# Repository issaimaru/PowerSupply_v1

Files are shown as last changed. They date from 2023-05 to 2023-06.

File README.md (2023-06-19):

# アズサ(Azusa)

<br>
 



<br>
この基板はJLCPCB様のFree PCB Sponsorshipにて制作しています．<br>

## Overview
  [MotorDriver-Controller_v4](https://github.com/TNCT-Mechatech/MotorDriver-Controller_v4)の機能+αと電源回路を合体させた統合型電源基板<br>
 
## Environments
&emsp;
&emsp;&emsp;
<br>

## Usage


1. [DriveUnit Bseries](https://github.com/Issaimaru/MoterDriver_v1)を使用したいチャネルのカードエッジコネクタに差し込む．<br>
1. モータードライバを差し込んだエッジコネクタと同じチャネルにモータを接続し，必要に応じて同じチャネルのコネクタにロータリーエンコーダを接続する．<br>
1. 非常停止スイッチを刺したコネクタの下にあるトグルスイッチをONに，それ以外のトグルスイッチをOFFにする．
1. XT90とUSB Type-Cからそれぞれ電源を供給し，非常停止スイッチをONにすると稼働する．
> **Note**<br>
> USB Type-C用電源を省略する方法はDescriptionsを参照<br>

## Features
<dl>
  <dt>通信プロトコル</dt>
  <dd>CAN with Flexible Data Rate(CAN FD)</dd>
  <dt>通信用コネクタ・ケーブル</dt>
  <dd>RJ-45/LANケーブル</dd>
  <dt>マイクロコンピュータ</dt>
  <dd>STM32F446RE</dd>
  <dt>特殊回路</dt>
  <dd>
  ・オートディスチャージ回路<br>
  ・車載用スローブローヒューズ

  <dt>保護回路(電源側)</dt>
  <dd>
  ・過電流保護(閾値可変)<br>
  ・ヒステリシス付き過熱保護<br>
  ・短絡保護<br>
  ・突入電流抑制<br>
  </dd>
  <dt>保護回路(信号側)</dt>
  <dd>
  ・過電圧保護<br>
  ・過電圧クランプ<br>
  ・突入電流抑制<br>
  ・過電流保護(東芝のeFuseを使用)<br>
  ・過熱保護<br>

## Descriptions
本ハードウェアの使用方法を詳しく書いていきます．<br>
質問や連絡等あれば[@TakenMaker](https://twitter.com/TakenMaker)までお願いします．<br>

### 回路図
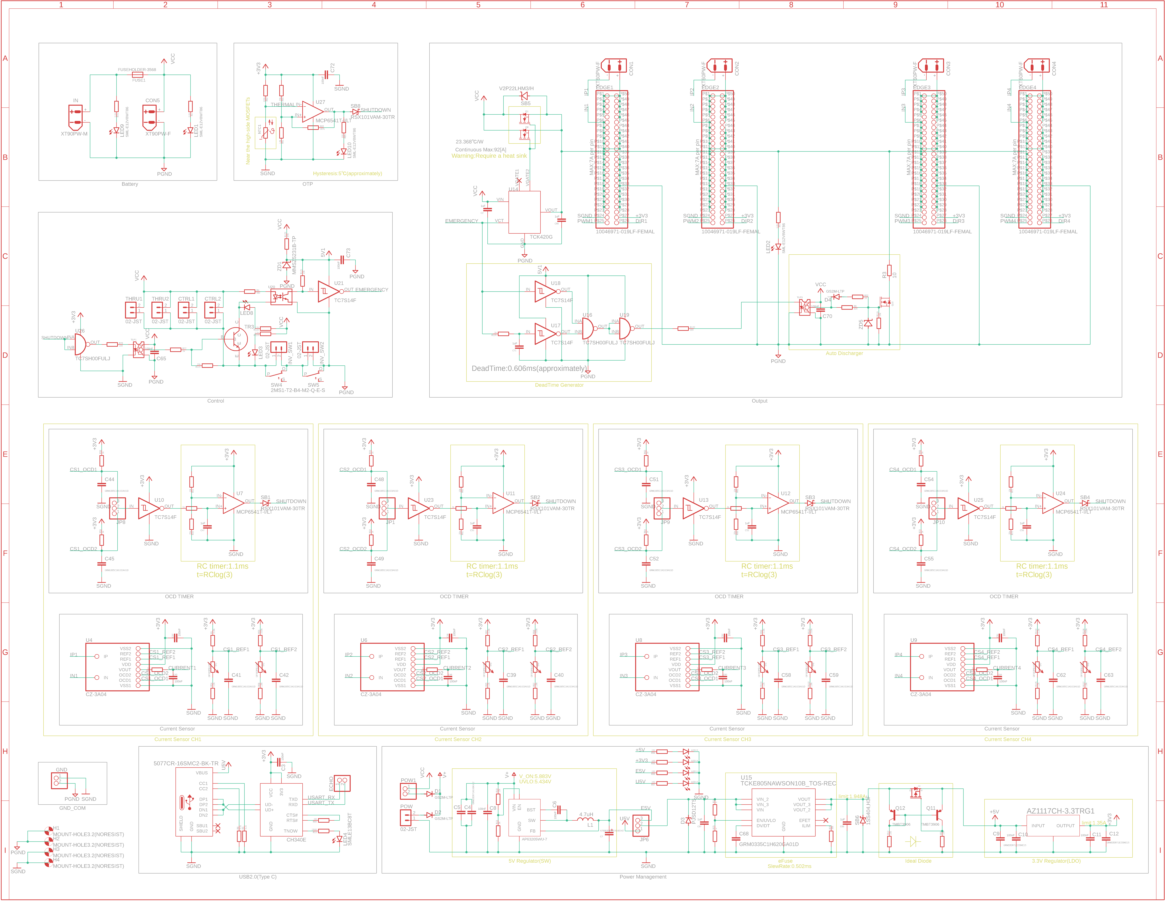
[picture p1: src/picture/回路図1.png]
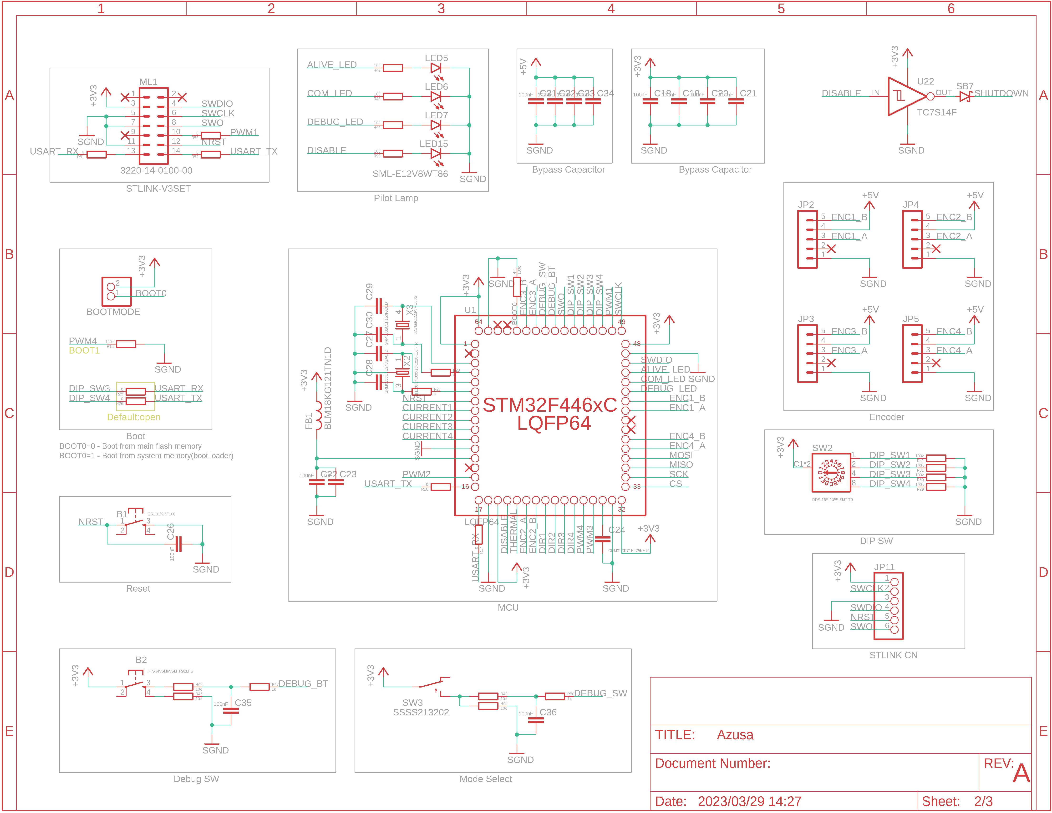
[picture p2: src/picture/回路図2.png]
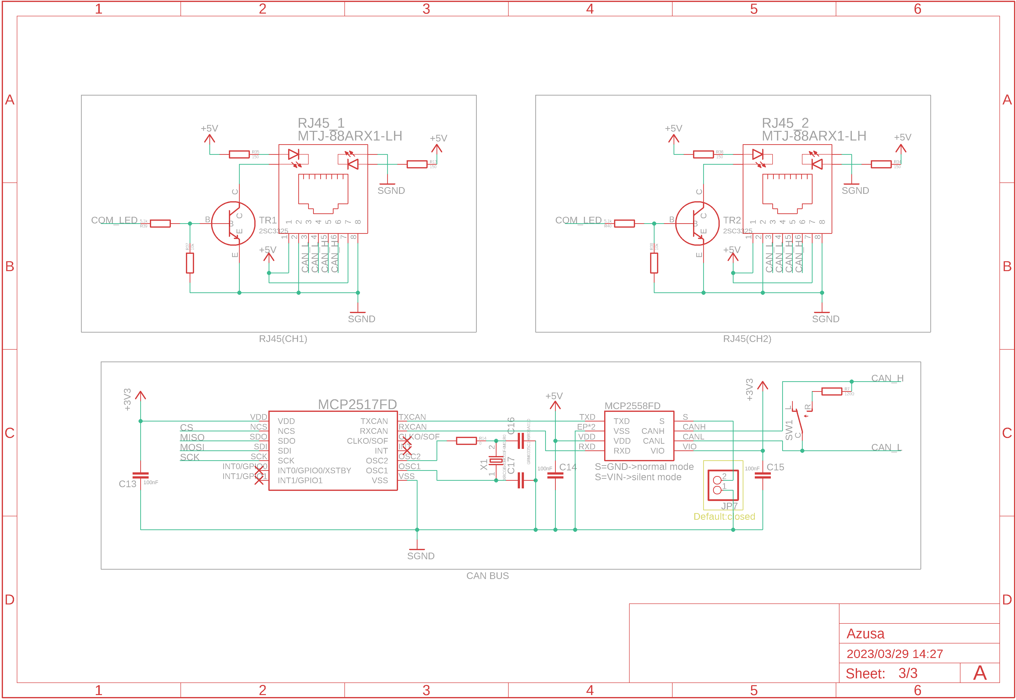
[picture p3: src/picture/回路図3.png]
&ensp;&ensp;

#### 始動方法
始動方法については[Usage](#usage)で示しました．<br>
ここでは始動時の応用的な使い方について紹介していきます．

- 信号用バッテリーの省略

<br>

JP6で信号用の電源をUSB給電or外部給電に切り替えることができます．<br>
外部電源としては，SPOWのピンに接続された電源かリポバッテリーか選ぶことができます．<br>
リポバッテリーの場合は「GND」と「SPOW」のピンヘッダを短絡してください．<br>
その際にE5VのLEDが点灯していることを確認してください．

## Bills of materials
> **Note**<br>
>最低限の部品のみここに書いています．<br>
>はんだ付けに必要な部品を調べるときは以下のexcelファイルを見るか，BOMファイルを出力してください．<br>
>[アズサ(Azusa)-ver2.0_必要部品.xlsx](src/%E3%82%A2%E3%82%BA%E3%82%B5(Azusa)-ver2.0_%E5%BF%85%E8%A6%81%E9%83%A8%E5%93%81.xlsx)
<br>
<dl>
  <dt>マイクロコンピュータ</dt>
  <dd>

  [STM32F446RET6](https://www.digikey.jp/ja/products/detail/stmicroelectronics/STM32F446RET6/5175962)

  </dd>

  <dt>電流センサ</dt>
  <dd>
  
  [CZ-3A04](https://www.digikey.jp/ja/products/detail/asahi-kasei-microdevices-akm/CZ3A04/11570562)

  </dd>
  <dt>CANトランシーバ</dt>
  <dd>

  [MCP2558FDT-H/MNY](https://www.digikey.jp/ja/products/detail/microchip-technology/MCP2558FDT-H-MNY/6009304)

  </dd>
  <dt>CANコントローラ</dt>
  <dd>

  [MCP2517FDT-H/SL](https://www.digikey.jp/ja/products/detail/microchip-technology/MCP2517FDT-H-SL/7801797)

  </dd>
  <dt>ヒートシンク</dt>
  <dd>
  
  [V2020B](https://www.digikey.jp/ja/products/detail/assmann-wsw-components/V2020B/8826902)
  
  </dd>
  <dt>ヒューズ</dt>
  <dd>

  [0297030.WXT](https://www.digikey.jp/en/products/detail/littelfuse-inc/0297030-WXT/5233697)

  </dd>
  <dt>USB・シリアル変換IC</dt>
  <dd>

  [CH340E](https://akizukidenshi.com/catalog/g/gI-13543/)

  </dd>
  <dt>NTCサーミスタ</dt>
  <dd>

  [NCU15WB473F60RC](https://www.digikey.jp/ja/products/detail/murata-electronics/NCU15WB473F60RC/9686720)

  </dd>
  <dt>DIPスイッチ</dt>
  <dd>

  [RDS-16S-1055-SMT-TR](https://www.digikey.jp/ja/products/detail/cui-devices/RDS-16S-1055-SMT-TR/12424507)

  </dd>
</dl>

## Contact
- Twitter [@TakenMaker](https://twitter.com/TakenMaker)

## Author
    
<table>
  <tr>
    <td align="center"><a href="https://github.com/Issaimaru">Issaimaru<br /></a>Issaimaru</td>
  </tr>
</table>
    
## Licence
  - Copyright © 2022-2023 Issaimaru<br>

本ハードウェアは，Apache License Version 2.0の下で配布されます．<br>
詳しくはLICENSEファイルをご確認ください．<br>

## 回路図のダウンロード(クローン)方法
1. Gitをインストールする．<br>Gitのインストール方法は[ここ](https://www.sejuku.net/blog/73444)を参照．
1. コマンドプロンプトを立ち上げる．
1. `cd ”ダウンロード先フォルダの絶対パス” `<br>
1. `git clone https://github.com/Issaimaru/PowerSupply_v1.git`<br>

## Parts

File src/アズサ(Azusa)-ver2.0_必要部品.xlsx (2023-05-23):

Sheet: 継続紙
財源（該当欄にチェックしてください） □授業料収入 □寄付金 □科学研究費 □受託研究 □共同研究 □運営費交付金 □
備考（予算科目等）
 | 請求者： |  |  |  | 納入場所：
品目（事項） 役務等の場合はその具体的内容 | 規格（内容） 規格は詳細に記入して下さい | 数量 |  | 単価 | 金額 | 備考
GCM188L81H104KA57 | 490-6049-1-ND | 100 | 個 | 8.81 | 881 | https://www.digikey.jp/ja/products/detail/murata-electronics/GCM188L81H104KA57D/2591908
GRM1885C1H102JA01D | 490-1451-1-ND | 100 | 個 | 3.12 | 312 | GRM1885C1H102JA01D Murata Electronics | コンデンサ | DigiKey (https://www.digikey.jp/ja/products/detail/murata-electronics/GRM1885C1H102JA01D/586943)
CR0603-JW-102ELF | CR0603-JW-102ELFCT-ND | 100 | 個 | 1.300 | 130 | CR0603-JW-102ELF Bourns Inc. | 抵抗器 | DigiKey (https://www.digikey.jp/ja/products/detail/bourns-inc/CR0603-JW-102ELF/3741004)
CR0603-JW-103ELF | CR0603-JW-103ELFCT-ND | 100 | 個 | 1.300 | 130 | https://www.digikey.jp/en/products/detail/bourns-inc/CR0603-JW-103ELF/3593214
SML-E12V8WT86 | 通販コード:I-11879 | 7 | パック | 140.000 | 980 | https://akizukidenshi.com/catalog/g/gI-11879/
CR0603-J/-000ELF | CR0603-J/-000ELFCT-ND | 100 | 個 | 0.760 | 76 | https://www.digikey.jp/ja/products/detail/bourns-inc/CR0603-J-000ELF/3593211
GRM21BC72A105KE01L | 490-14464-1-ND | 100 | 個 | 21.390 | 2139 | https://www.digikey.jp/en/products/detail/murata-electronics/GRM21BC72A105KE01L/6606093
シュミットトリガインバータ ＴＣ７Ｓ１４Ｆ | 通販コード:I-14737 | 8 | 個 | 60.000 | 480 | https://akizukidenshi.com/catalog/g/gI-14737/
半固定ボリューム ＧＦ０６３Ｐ | 通販コード:P-14905 | 50 | 個 | 30.000 | 1500 | 半固定ボリューム ＧＦ０６３Ｐ １０ｋΩ: パーツ一般 秋月電子通商-電子部品・ネット通販 (akizukidenshi.com) (https://akizukidenshi.com/catalog/g/gP-14905/)
CR0603-JW-151ELF | CR0603-JW-151ELFCT-ND | 100 | 個 | 1.410 | 141 | CR0603-JW-151ELF Bourns Inc. | 抵抗器 | DigiKey (https://www.digikey.jp/ja/products/detail/bourns-inc/CR0603-JW-151ELF/3784293)
CR0603-JW-104ELF | CR0603-JW-104ELFCT-ND | 100 | 個 | 0.760 | 76 | CR0603-JW-104ELF Bourns Inc. | 抵抗器 | DigiKey (https://www.digikey.jp/ja/products/detail/bourns-inc/CR0603-JW-104ELF/2345098)
CR0603-JW-101ELF | CR0603-JW-101ELFCT-ND | 100 | 個 | 1.300 | 130 | CR0603-JW-101ELF Bourns Inc. | 抵抗器 | DigiKey (https://www.digikey.jp/ja/products/detail/bourns-inc/CR0603-JW-101ELF/3741003)
RSX101VAM-30TR | 通販コード:RSX101VAM-30TR | 2 | 個 | 180.000 | 360 | ショットキーバリアダイオード ＲＳＸ１０１ＶＡＭ－３０ ３０Ｖ１Ａ（２０個入）: 半導体(モジュール) 秋月電子通商-電子部品・ネット通販 (akizukidenshi.com) (https://akizukidenshi.com/catalog/g/gI-05951/)
MCP6541T-I/LT | MCP6541T-I/LTCT-ND | 100 | 個 | 48.990 | 4899 | MCP6541T-I/LT Microchip Technology | Integrated Circuits (ICs) | DigiKey (https://www.digikey.jp/en/products/detail/microchip-technology/MCP6541T-I-LT/551750)
CR0603-JW-112ELF | CR0603-JW-112ELFCT-ND | 100 | 個 | 1.410 | 141 | CR0603-JW-112ELF Bourns Inc. | 抵抗器 | DigiKey (https://www.digikey.jp/ja/products/detail/bourns-inc/CR0603-JW-112ELF/3784271)
CR0603-JW-512ELF | 118-CR0603-JW-512ELFCT-ND | 100 | 個 | 1.410 | 141 | CR0603-JW-512ELF Bourns Inc. | 抵抗器 | DigiKey (https://www.digikey.jp/ja/products/detail/bourns-inc/CR0603-JW-512ELF/3784394)
CR0603-J/-3R3ELF | CR0603-J/-3R3ELFCT-ND | 100 | 個 | 1.410 | 141 | https://www.digikey.jp/ja/products/detail/bourns-inc/CR0603-J-3R3ELF/3784247
CR0603-JW-203ELF | CR0603-JW-203ELFCT-ND | 100 | 個 | 1.410 | 141 | https://www.digikey.jp/ja/products/detail/bourns-inc/CR0603-JW-203ELF/3741006
CR0603-FX-1582ELF | CR0603-FX-1582ELFCT-ND | 100 | 個 | 1.050 | 105 | CR0603-FX-1582ELF Bourns Inc. | 抵抗器 | DigiKey (https://www.digikey.jp/ja/products/detail/bourns-inc/CR0603-FX-1582ELF/3783757)
CR0603-FX-1182ELF | 118-CR0603-FX-1182ELFCT-ND | 100 | 個 | 1.480 | 148 | CR0603-FX-1182ELF Bourns Inc. | 抵抗器 | DigiKey (https://www.digikey.jp/ja/products/detail/bourns-inc/CR0603-FX-1182ELF/3783693)
CR0603-JW-162ELF | CR0603-JW-162ELFCT-ND | 100 | 個 | 1.410 | 141 | CR0603-JW-162ELF Bourns Inc. | 抵抗器 | DigiKey (https://www.digikey.jp/ja/products/detail/bourns-inc/CR0603-JW-162ELF/3784303)
CR0603-JW-122ELF | 118-CR0603-JW-122ELFCT-ND | 100 | 個 | 1.050 | 105 | CR0603-JW-122ELF Bourns Inc. | 抵抗器 | DigiKey (https://www.digikey.jp/ja/products/detail/bourns-inc/CR0603-JW-122ELF/3784278)
TC7SH00FULJ(CB | 通販コード:I-15748 | 2 | 個 | 100.000 | 200 | ２入力ＮＡＮＤ ＴＣ７ＳＨ００ＦＵ（１０個入）: 半導体(モジュール) 秋月電子通商-電子部品・ネット通販 (akizukidenshi.com) (https://akizukidenshi.com/catalog/g/gI-15748/)
SQJA16EP-T1_GE3 | 742-SQJA16EP-T1_GE3CT-ND | 15 | 個 | 198.900 | 2983.5 | SQJA16EP-T1_GE3 Vishay Siliconix | ディスクリート半導体製品 | DigiKey (https://www.digikey.jp/ja/products/detail/vishay-siliconix/SQJA16EP-T1-GE3/14542661)
GS2M-LTP | GS2M-LTPMSCT-ND | 20 | 個 | 31.700 | 634 | GS2M-LTP Micro Commercial Co | ディスクリート半導体製品 | DigiKey (https://www.digikey.jp/ja/products/detail/micro-commercial-co/GS2M-LTP/3775006)
２ＳＣ３３２５－Ｙ ５０Ｖ５００ｍＡ | 通販コード:I-00628 | 1 | 個 | 100.000 | 100 | チップトランジスタ ２ＳＣ３３２５－Ｙ ５０Ｖ５００ｍＡ （２０個入）: 半導体(モジュール) 秋月電子通商-電子部品・ネット通販 (akizukidenshi.com) (https://akizukidenshi.com/catalog/g/gI-00628/)
TMBT3906,LM | TMBT3906LMCT-ND | 10 | 個 | 22.700 | 227 | TMBT3906,LM Toshiba Semiconductor and Storage | Discrete Semiconductor Products | DigiKey (https://www.digikey.jp/en/products/detail/toshiba-semiconductor-and-storage/TMBT3906-LM/5403461)
TLP152(TPL_E | 通販コード:I-10824 | 10 | 個 | 80.000 | 800 | フォトカプラ ＧａＡｌＡｓ赤外ＬＥＤ＋フォトＩＣ ＴＬＰ１５２: 半導体(モジュール) 秋月電子通商-電子部品・ネット通販 (akizukidenshi.com) (https://akizukidenshi.com/catalog/g/gI-10824/)
GRM32ER71H106KA12 | 通販コード:P-16113 | 2 | 個 | 200.000 | 400 | チップ積層セラミックコンデンサー １０μＦ５０Ｖ Ｘ７Ｒ ３２２５ （５個入）: パーツ一般 秋月電子通商-電子部品・ネット通販 (akizukidenshi.com) (https://akizukidenshi.com/catalog/g/gP-16113/)
GRM32ER71E226KE15 | 通販コード:P-06047 | 2 | 個 | 250.000 | 500 | チップ積層セラミックコンデンサー ２２μＦ２５Ｖ Ｘ７Ｒ ３２２５ （５個入）: パーツ一般 秋月電子通商-電子部品・ネット通販 (akizukidenshi.com) (https://akizukidenshi.com/catalog/g/gP-06047/)
GRM0335C1H6R0BA01D | 490-11339-1-ND | 10 | 個 | 2.200 | 22 | GRM0335C1H6R0BA01D Murata Electronics | Capacitors | DigiKey (https://www.digikey.jp/en/products/detail/murata-electronics/GRM0335C1H6R0BA01D/4358772)
GRM0335C1H150FA01D | 490-GRM0335C1H150FA01DCT-ND | 10 | 個 | 4.600 | 46 | GRM0335C1H150FA01D Murata Electronics | Capacitors | DigiKey (https://www.digikey.jp/en/products/detail/murata-electronics/GRM0335C1H150FA01D/11618577)
GRM0335C1E240GA01D | 490-11289-1-ND | 10 | 個 | 1.800 | 18 | GRM0335C1E240GA01D Murata Electronics | Capacitors | DigiKey (https://www.digikey.jp/en/products/detail/murata-electronics/GRM0335C1E240GA01D/4358594)
2MS1-T2-B4-M2-Q-E-S | 通販コード:P-12406 | 10 | 個 | 90.000 | 900 | 基板用小型３Ｐトグルスイッチ １回路２接点: パーツ一般 秋月電子通商-電子部品・ネット通販 (akizukidenshi.com) (https://akizukidenshi.com/catalog/g/gP-12406/)
XRCGB40M000F4M01R0 | 通販コード:490-18350-1-ND | 10 | 個 | 35.200 | 352 | XRCGB40M000F4M01R0 Murata Electronics | 水晶発振器、発振器、共振器 | DigiKey (https://www.digikey.jp/ja/products/detail/murata-electronics/XRCGB40M000F4M01R0/9959707)
V2P22LHM3/H | 112-V2P22LHM3/HCT-ND | 10 | 個 | 46.800 | 468 | V2P22LHM3/H Vishay General Semiconductor - Diodes Division | Discrete Semiconductor Products | DigiKey (https://www.digikey.jp/en/products/detail/vishay-general-semiconductor-diodes-division/V2P22LHM3-H/10638949)
TLP293(BLL-TPLE(T | 通販コード:I-16783 | 2 | 個 | 120.000 | 240 | https://akizukidenshi.com/catalog/g/gI-16783/
TCK420G,L3F | 264-TCK420GL3FCT-ND | 10 | 個 | 104.800 | 1048 | TCK420G,L3F Toshiba Semiconductor and Storage | Integrated Circuits (ICs) | DigiKey (https://www.digikey.jp/en/products/detail/toshiba-semiconductor-and-storage/TCK420G-L3F/16516790)
SSSS213202 | 通販コード:P-05043 | 1 | 個 | 330.000 | 330 | 表面実装用スライドスイッチ ＳＳＳＳ２１３２０２ （１０個入）: パーツ一般 秋月電子通商-電子部品・ネット通販 (akizukidenshi.com) (https://akizukidenshi.com/catalog/g/gP-05043/)
SSM3J332R | 通販コード:I-15985 | 1 | 個 | 120.000 | 120 | ＰｃｈＭＯＳＦＥＴ ＳＳＭ３Ｊ３３２Ｒ （１０個入）: 半導体(モジュール) 秋月電子通商-電子部品・ネット通販 (akizukidenshi.com) (https://akizukidenshi.com/catalog/g/gI-15985/)
SS-12SDP2 | 通販コード:P-15643 | 5 | 個 | 80.000 | 400 | スライドスイッチ １回路２接点: パーツ一般 秋月電子通商-電子部品・ネット通販 (akizukidenshi.com) (https://akizukidenshi.com/catalog/g/gP-15643/)
SMLE13BC8T | 通販コード:I-11881 | 2 | 個 | 150.000 | 300 | 青色チップＬＥＤ １６０８サイズ ＳＭＬＥ１３ＢＣ８ＴＴ８６ （１０個入）: LED(発光ダイオード) 秋月電子通商-電子部品・ネット通販 (akizukidenshi.com) (https://akizukidenshi.com/catalog/g/gI-11881)
RH100-24.000-18-1020-EXT-TR | 2151-RH100-24.000-18-1020-EXT-TRCT-ND | 10 | 個 | 28.300 | 283 | RH100-24.000-18-1020-EXT-TR Raltron Electronics | Crystals, Oscillators, Resonators | DigiKey (https://www.digikey.jp/en/products/detail/raltron-electronics/RH100-24-000-18-1020-EXT-TR/15963323)
RDS-16S-1055-SMT-TR | 2223-RDS-16S-1055-SMT-ND | 6 | 個 | 392.000 | 2352 | RDS-16S-1055-SMT CUI Devices | Switches | DigiKey (https://www.digikey.jp/en/products/detail/cui-devices/RDS-16S-1055-SMT/12424498)
PTS645SM95SMTR92LFS | CKN10822CT-ND | 10 | 個 | 43.800 | 438 | PTS645SM95SMTR92LFS C&K | Switches | DigiKey (https://www.digikey.jp/en/products/detail/c-k/PTS645SM95SMTR92LFS/7056044)
PJSD12TS | 3757-PJSD12TS_R1_00001CT-ND | 10 | 個 | 30.7 | 307 | PJSD12TS_R1_00001 Panjit International Inc. | 回路保護 | DigiKey (https://www.digikey.jp/ja/products/detail/panjit-international-inc/PJSD12TS-R1-00001/14660201)
NCU15WB473F60RC | 490-18155-1-ND | 6 | 個 | 9.6 | 57.6 | https://www.digikey.jp/ja/products/detail/murata-electronics/NCU15WB473F60RC/9686720
MMSZ5231B-TP | MMSZ5231B-TPMSCT-ND | 10 | 個 | 22.8 | 228 | MMSZ5231B-TP Micro Commercial Co | Discrete Semiconductor Products | DigiKey (https://www.digikey.jp/en/products/detail/micro-commercial-co/MMSZ5231B-TP/1793201)
MMBZ5248B-TP | MMBZ5248B-TPMSCT-ND | 10 | 個 | 22.1 | 221 | MMBZ5248B-TP Micro Commercial Co | Discrete Semiconductor Products | DigiKey (https://www.digikey.jp/en/products/detail/micro-commercial-co/MMBZ5248B-TP/2213597)
GRM31CR71H475KA12 | 490-6521-1-ND | 10 | 個 | 38.9 | 389 | GRM31CR71H475KA12L Murata Electronics | Capacitors | DigiKey (https://www.digikey.jp/en/products/detail/murata-electronics/GRM31CR71H475KA12L/2548209)
GRM0335C1H620GA01D | 490-11337-1-ND | 10 | 個 | 1.8 | 18 | GRM0335C1H620GA01D Murata Electronics | Capacitors | DigiKey (https://www.digikey.jp/en/products/detail/murata-electronics/GRM0335C1H620GA01D/4358769)
FUSEHOLDER-3568 | 36-3568-ND | 10 | 個 | 186 | 1860 | 3568 Keystone Electronics | Circuit Protection | DigiKey (https://www.digikey.jp/en/products/detail/keystone-electronics/3568/2137306)
0297030.WXT | 0297030.WXT-ND | 10 | 個 | 34.6 | 346 | 0297030.WXT Littelfuse Inc. | Circuit Protection | DigiKey (https://www.digikey.jp/en/products/detail/littelfuse-inc/0297030-WXT/5233697)
CH340E | 通販コード:I-13543 | 10 | 個 | 70 | 700 | ＵＳＢ・シリアル変換ＩＣ ＣＨ３４０Ｅ: 半導体(モジュール) 秋月電子通商-電子部品・ネット通販 (akizukidenshi.com) (https://akizukidenshi.com/catalog/g/gI-13543/)
BLM18KG121TN1D | 490-5254-1-ND | 10 | 個 | 11.2 | 112 | BLM18KG121TN1D Murata Electronics | Filters | DigiKey (https://www.digikey.jp/en/products/detail/murata-electronics/BLM18KG121TN1D/1982762)
AZ1117CH-3.3TRG1 | 通販コード:I-16155 | 30 | 個 | 30 | 900 | 三端子レギュレーター ３．３Ｖ ＡＺ１１１７ＣＨ－３．３ＴＲＧ１: 半導体(モジュール) 秋月電子通商-電子部品・ネット通販 (akizukidenshi.com) (https://akizukidenshi.com/catalog/g/gI-16155/)
A768EB566M1VLAE042 | 399-A768EB566M1VLAE042CT-ND | 10 | 個 | 51.7 | 517 | A768EB566M1VLAE042 KEMET | コンデンサ | DigiKey (https://www.digikey.jp/ja/products/detail/kemet/A768EB566M1VLAE042/13420147)
5077CR-16SMC2-BK-TR | 通販コード:C-14356 | 5 | 個 | 110 | 550 | ＵＳＢ Ｔｙｐｅ－Ｃコネクタ 基板用: パーツ一般 秋月電子通商-電子部品・ネット通販 (akizukidenshi.com) (https://akizukidenshi.com/catalog/g/gC-14356/)
NRS5030T4R7MMGJ | 587-3461-1-ND | 10 | 個 | 41.9 | 419 | NRS5030T4R7MMGJ Taiyo Yuden | Inductors, Coils, Chokes | DigiKey (https://www.digikey.jp/en/products/detail/taiyo-yuden/NRS5030T4R7MMGJ/4157849)
3220-14-0100-00 | 1175-1630-ND | 10 | 個 | 90.8 | 908 | 3220-14-0100-00 CNC Tech | コネクタ、相互接続 | DigiKey (https://www.digikey.jp/ja/products/detail/cnc-tech/3220-14-0100-00/3883664)
32.768K12.5PI/MC306 | 3155-32.768K12.5PI/MC306CT-ND | 5 | 個 | 34 | 170 | 32.768K12.5PI/MC306 YIC | 水晶発振器、発振器、共振器 | DigiKey (https://www.digikey.jp/ja/products/detail/yic/32-768K12-5PI-MC306/15648602)
1SS404,H3F | 1SS404H3FCT-ND | 5 | 個 | 28 | 140 | 1SS404,H3F Toshiba Semiconductor and Storage | Discrete Semiconductor Products | DigiKey (https://www.digikey.jp/en/products/detail/toshiba-semiconductor-and-storage/1SS404-H3F/4304883)
CR0603-JW-821ELF | CR0603-JW-821ELFCT-ND | 10 | 個 | 2.8 | 28 | CR0603-JW-821ELF Bourns Inc. | 抵抗器 | DigiKey (https://www.digikey.jp/ja/products/detail/bourns-inc/CR0603-JW-821ELF/3784429)
CR0603-JW-563ELF | CR0603-JW-563ELFCT-ND | 10 | 個 | 2.8 | 28 | CR0603-JW-563ELF Bourns Inc. | 抵抗器 | DigiKey (https://www.digikey.jp/ja/products/detail/bourns-inc/CR0603-JW-563ELF/3784403)
CR0603-JW-561ELF | 118-CR0603-JW-561ELFCT-ND | 10 | 個 | 2.9 | 29 | CR0603-JW-561ELF Bourns Inc. | 抵抗器 | DigiKey (https://www.digikey.jp/ja/products/detail/bourns-inc/CR0603-JW-561ELF/3784399)
CR0603-JW-302ELF | 118-CR0603-JW-302ELFCT-ND | 10 | 個 | 2.1 | 21 | CR0603-JW-302ELF Bourns Inc. | 抵抗器 | DigiKey (https://www.digikey.jp/ja/products/detail/bourns-inc/CR0603-JW-302ELF/3784351)
CR0603-JW-333ELF | CR0603-JW-333ELFCT-ND | 10 | 個 | 2.9 | 29 | CR0603-JW-333ELF Bourns Inc. | 抵抗器 | DigiKey (https://www.digikey.jp/ja/products/detail/bourns-inc/CR0603-JW-333ELF/2345099)
CR0603-JW-301ELF | CR0603-JW-301ELFCT-ND | 10 | 個 | 2.7 | 27 | CR0603-JW-301ELF Bourns Inc. | 抵抗器 | DigiKey (https://www.digikey.jp/ja/products/detail/bourns-inc/CR0603-JW-301ELF/3784350)
CR0603-JW-271ELF | 118-CR0603-JW-271ELFCT-ND | 10 | 個 | 2.8 | 28 | https://www.digikey.jp/ja/products/detail/bourns-inc/CR0603-JW-271ELF/3784341
CR0603-FX-1873ELF | 118-CR0603-FX-1873ELFCT-ND | 10 | 個 | 2.9 | 29 | CR0603-FX-1873ELF Bourns Inc. | 抵抗器 | DigiKey (https://www.digikey.jp/ja/products/detail/bourns-inc/CR0603-FX-1873ELF/3783803)
CR0603-JW-151ELF | CR0603-JW-151ELFCT-ND | 10 | 個 | 2.8 | 28 | CR0603-JW-151ELF Bourns Inc. | 抵抗器 | DigiKey (https://www.digikey.jp/ja/products/detail/bourns-inc/CR0603-JW-151ELF/3784293)
CR0603-JW-123ELF | 118-CR0603-JW-123ELFCT-ND | 10 | 個 | 2.7 | 27 | CR0603-JW-123ELF Bourns Inc. | 抵抗器 | DigiKey (https://www.digikey.jp/ja/products/detail/bourns-inc/CR0603-JW-123ELF/3784280)
CR0603-FX-1200ELF | CR0603-FX-1200ELFCT-ND | 10 | 個 | 2.1 | 21 | CR0603-FX-1200ELF Bourns Inc. | 抵抗器 | DigiKey (https://www.digikey.jp/ja/products/detail/bourns-inc/CR0603-FX-1200ELF/3783698)
CR0603-JW-100ELF | 118-CR0603-JW-100ELFCT-ND | 10 | 個 | 2.9 | 29 | CR0603-JW-100ELF Bourns Inc. | 抵抗器 | DigiKey (https://www.digikey.jp/ja/products/detail/bourns-inc/CR0603-JW-100ELF/3784261)
CR0603-JW-182ELF | 118-CR0603-JW-182ELFCT-ND | 10 | 個 | 2.8 | 28 | CR0603-JW-182ELF Bourns Inc. | 抵抗器 | DigiKey (https://www.digikey.jp/ja/products/detail/bourns-inc/CR0603-JW-182ELF/3784311)
RSMF2JT10R0 | RSMF2JT10R0CT-ND | 10 | 個 | 34.2 | 342 | RSMF2JT10R0 Stackpole Electronics Inc | 抵抗器 | DigiKey (https://www.digikey.jp/ja/products/detail/stackpole-electronics-inc/RSMF2JT10R0/1694892)
XT60PW-F | XT60PW-F | 50 | 個 | 93.64 | 4682 | XT60PW-F AMASS - ソケット | DC電源; XT60; メス; PIN: 2; 基板マウント用; THT; メッキ: gold flash; 黄色; 30A | TME - 電子部品 (https://www.tme.com/jp/ja/details/xt60pw-f/dcdian-yuan-konekuta/amass/)
XT90PW-F | XT90PW-F | 20 | 個 | 159.19 | 3183.8 | XT90PW-F AMASS - ソケット | DC電源; XT90; メス; PIN: 2; 基板マウント用; THT; メッキ: gold flash; 黄色; 40A | TME - 電子部品 (https://www.tme.com/jp/ja/details/xt90pw-f/dcdian-yuan-konekuta/amass/)
XT90PW-M | XT90PW-M | 20 | 個 | 159.19 | 3183.8 | XT90PW-M AMASS - Socket | DC supply; XT90; male; PIN: 2; on PCBs; THT; yellow; 40A; 500V | TME - Electronic components (https://www.tme.com/us/en-us/details/xt90pw-m/dc-power-connectors/amass/)
合計 |  |  |  |  | 46044.7

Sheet: 記入例
財源（該当欄にチェックしてください） □授業料収入 □寄付金 □科学研究費 □受託研究 □共同研究 □運営費交付金 □
 | 教員研究経費
備考（予算科目等）
 | 請求者： | ○○太郎 |  |  | 納入場所： | ○○教員室
品目（事項） 役務等の場合はその具体的内容 | 規格（内容） 規格は詳細に記入して下さい | 数量 |  | 単価 | 金額 | 備考
フラットファイル | KOKUYO A4ﾀﾃ ﾌ-V10 青(B) | 5 | 冊
〃 | KOKUYO A4ﾖｺ ﾌ-V15 緑(G) | 2 | 冊
リサーチラボノート〈ＳＤ〉 | KOKUYO ﾉ-LB208S | 3 | 冊
鉛筆（ＨＢ） | TOMBOW 木物語 LA-KEAHB | 1 | 打

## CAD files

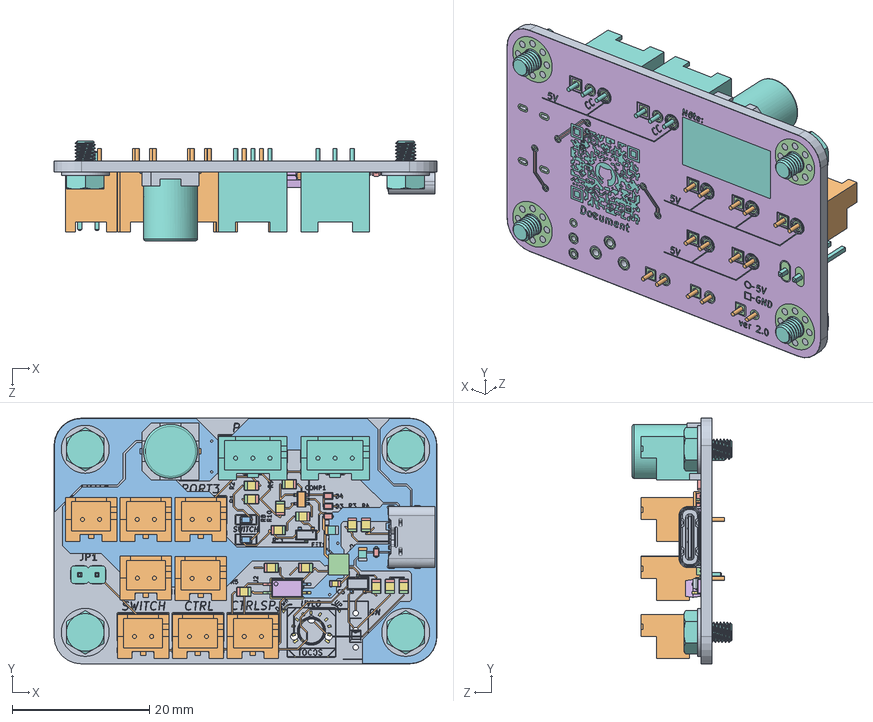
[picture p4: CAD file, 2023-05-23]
src/(KiCad)Azusa/src/SolidWorks/USB_JST-XH_Converter組立図.SLDASM
55.9 x 35.8 x 14.5 mm
Pcb_f1fe
topTracks_f1fe
topZones_f1fe
botPads_f1fe
botTracks_f1fe
botZones_f1fe
bottopSilks_f115
botSilks_30d3
USB1_CUI_DEVICES_UJC-HP-3-SMT-TR_639B4C46
PORT1_B02B-XASK-1_639C336B x 8
SW2_SMLE1_639B495B x 2
RT1220P-101-M x 14
RT1220P-101-M001 x 14
RT1220P-101-M002 x 14
RT1220P-101-M003 x 14
CAP_GCM21B_MUR x 2
CAP_GCM21B_MUR001 x 2
CAP_GCM21B_MUR002 x 2
TLP293(E
TLP293(E001
TLP293(E002
TLP293(E003
TLP293(E004
JP1_PinHeader_1x02_P254mm_Vertical_639B4B42
S-Mini-ZKN
S-Mini-ZKN001
S-Mini-ZKN002
S-Mini-ZKN003
1N914BWT x 4
1N914BWT001 x 4
1N914BWT002 x 4
1N914BWT003 x 4
POWER_B03B-XASK-1_639B4BD1 x 2
PinsArrayL
PinsArrayL001
FilletPinR
GQM1885C1H8R2CB01J
GQM1885C1H8R2CB01J001
GQM1885C1H8R2CB01J002
U2-P_NCH(繝輔ぅ繝ｬ繝・ヨ蠕・
U2-P_NCH(繝輔ぅ繝ｬ繝・ヨ蠕・001
U2-P_NCH(繝輔ぅ繝ｬ繝・ヨ蠕・002
U2-P_NCH(繝輔ぅ繝ｬ繝・ヨ蠕・003
WSON10B_Assy_new_ver2
WSON10B_Assy_new_ver003
WSON10B_Assy_new_ver004
WSON10B_Assy_new_ver005
WSON10B_Assy_new_ver006
WSON10B_Assy_new_ver007
WSON10B_Assy_new_ver008
WSON10B_Assy_new_ver009
WSON10B_Assy_new_ver010
WSON10B_Assy_new_ver011
WSON10B_Assy_new_ver012
WSON10B_Assy_new_ver013
M3×10 x 4
平座金 x 4

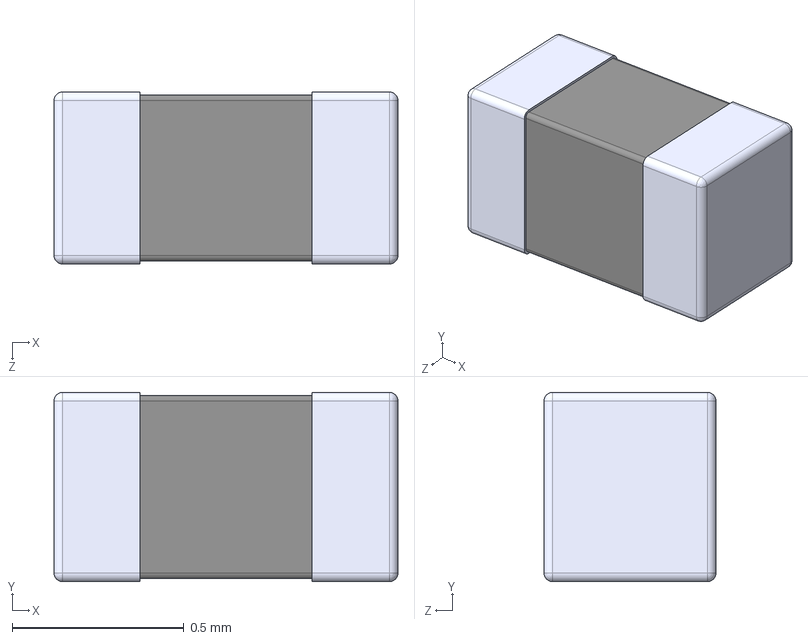
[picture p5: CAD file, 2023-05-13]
src/(KiCad)Azusa/3dmodels/NCU15WB473F60RC.step
1.00 x 0.55 x 0.5 mm

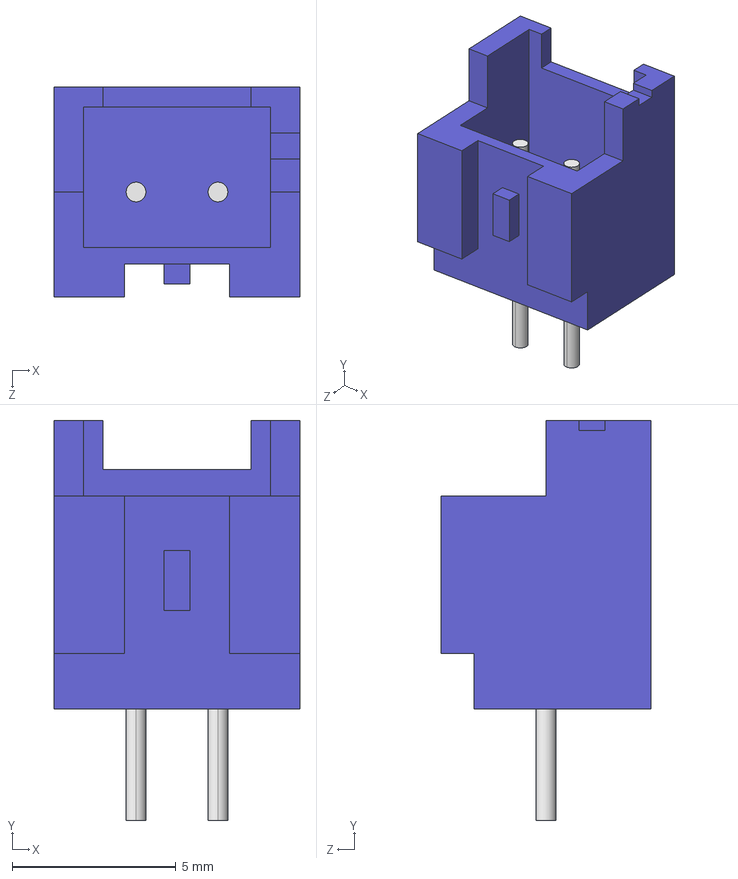
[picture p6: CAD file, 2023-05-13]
src/(KiCad)Azusa/3dmodels/B02B-XASK-1.STEP
7.50 x 12.2 x 6.40 mm

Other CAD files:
src/(KiCad)Azusa/src/SolidWorks/C3_GQM1885C1H8R2CB01J003_639B4C15.SLDASM
src/(KiCad)Azusa/src/SolidWorks/C4_U2-P_NCH(繝輔ぅ繝ｬ繝・ヨ蠕・004_639B4C24.SLDASM
src/(KiCad)Azusa/src/SolidWorks/Board_Geoms_f1fe.SLDASM
src/(KiCad)Azusa/src/SolidWorks/WSON10B_Assy_new_ver013.SLDPRT
src/(KiCad)Azusa/src/SolidWorks/TR1_S-Mini-ZKN004_639B4B58.SLDASM
src/(KiCad)Azusa/src/SolidWorks/Top_f1fe_1.SLDASM
src/(KiCad)Azusa/src/SolidWorks/PinsArrayL002.SLDASM
src/(KiCad)Azusa/src/SolidWorks/Step_Models_f1fe.SLDASM
src/(KiCad)Azusa/src/SolidWorks/FET1_ASSEMBLY_639B4C0B.SLDASM
src/(KiCad)Azusa/src/SolidWorks/C1_CAP_GCM21B_MUR003_639B4A01.SLDASM
src/(KiCad)Azusa/src/SolidWorks/COMP1_part007_639B4BA4.SLDASM
src/(KiCad)Azusa/src/SolidWorks/U2_TLP293(E005_639B4A97.SLDASM
src/(KiCad)Azusa/src/SolidWorks/D2_1N914BWT004_639B4B74.SLDASM
src/(KiCad)Azusa/src/SolidWorks/R2_RT1220P-101-M004_639B496B.SLDASM
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

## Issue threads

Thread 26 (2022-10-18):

ver1.0における不具合，設計のガバ

Issaimaru, 2022-10-18:
- [ ] 非常停止スイッチが押された後平滑コンデンサの容量分だけ駆動してしまう

Issaimaru, 2022-10-18:
非常停止スイッチが押された後平滑コンデンサの容量分だけ駆動してしまう問題の対処法(?)<br>
[さばねっこさんの記事](https://sabanekko2.hatenablog.com/entry/2022/03/10/224528)<br>
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

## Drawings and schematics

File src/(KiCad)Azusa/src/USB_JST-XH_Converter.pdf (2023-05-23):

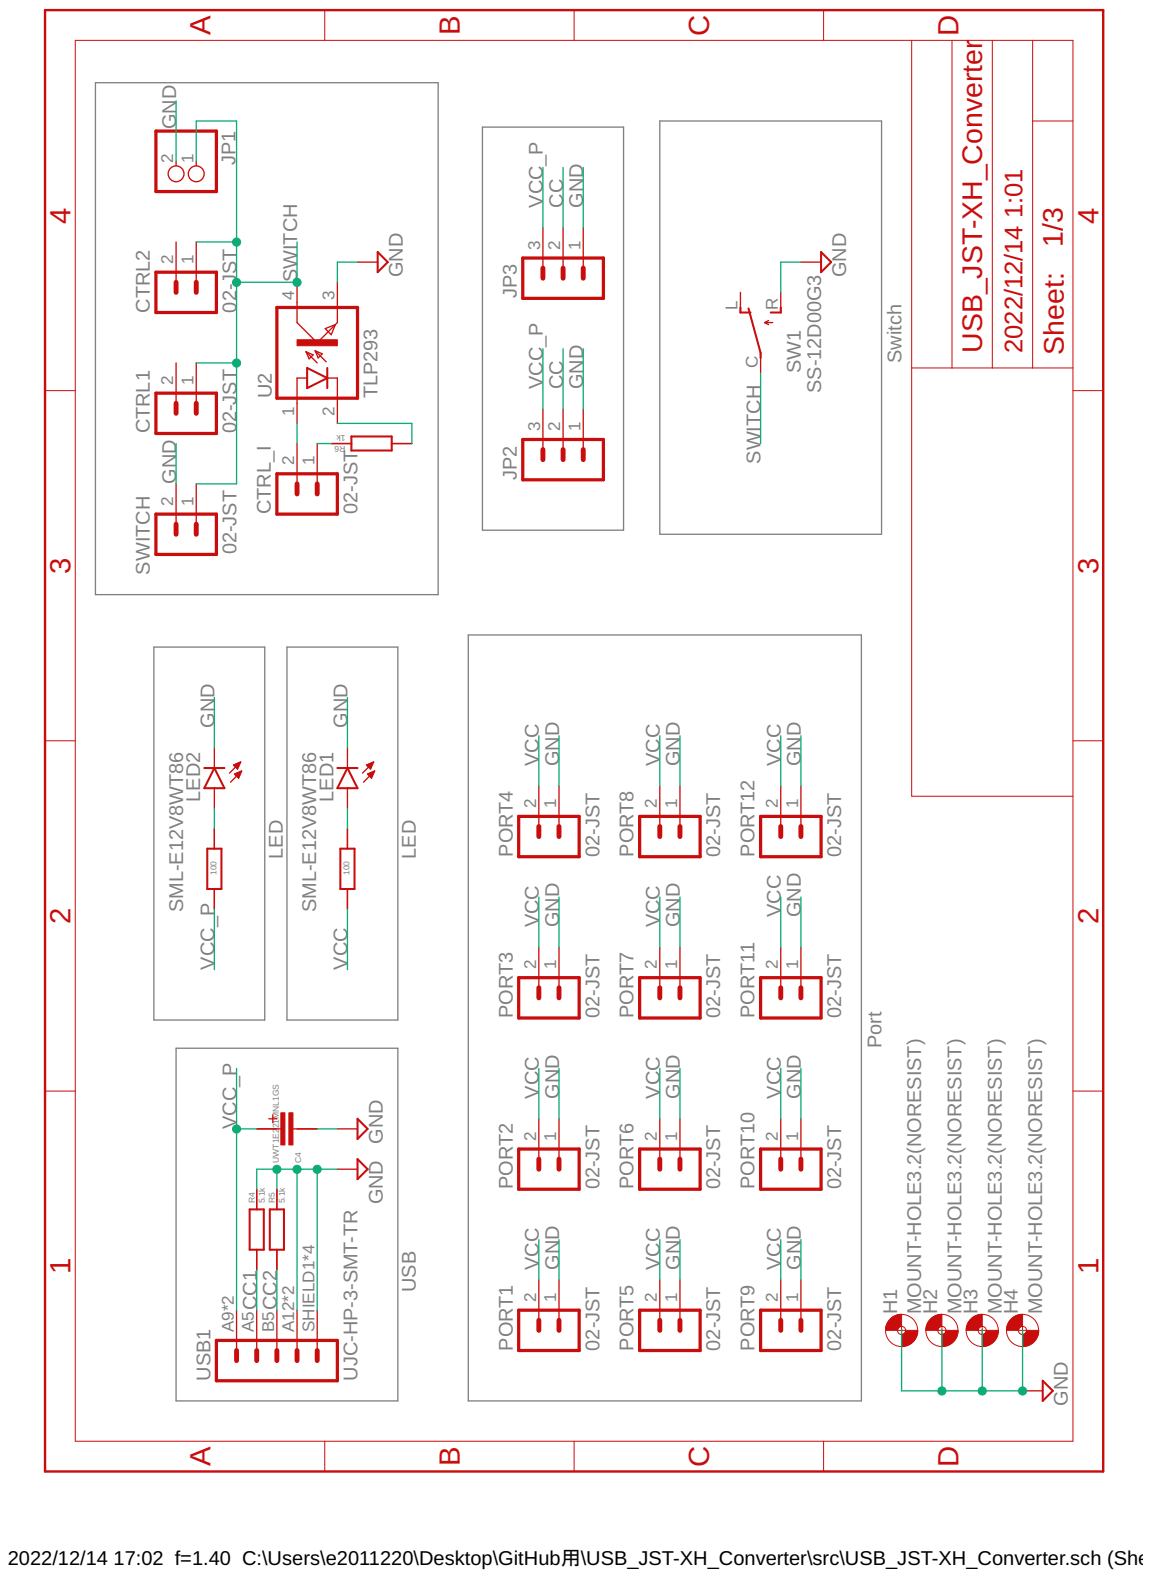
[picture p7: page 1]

2022/12/14 17:02 f=1.40 C:\Users\e2011220\Desktop\GitHub用\USB_JST-XH_Converter\src\USB_JST-XH_Converter.sch (Sheet: 1/3)

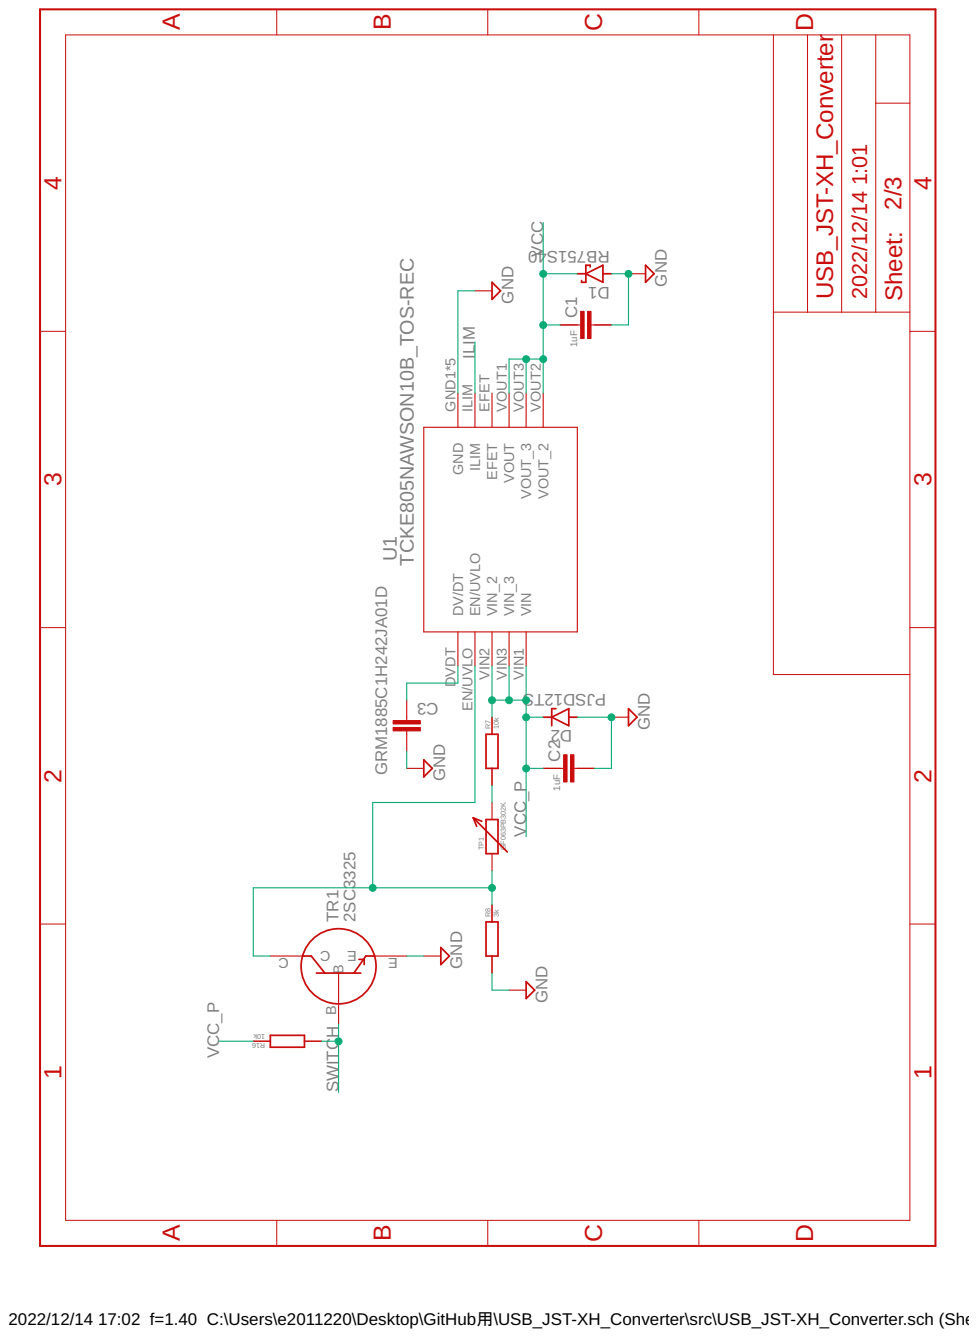
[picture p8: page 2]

2022/12/14 17:02 f=1.40 C:\Users\e2011220\Desktop\GitHub用\USB_JST-XH_Converter\src\USB_JST-XH_Converter.sch (Sheet: 2/3)

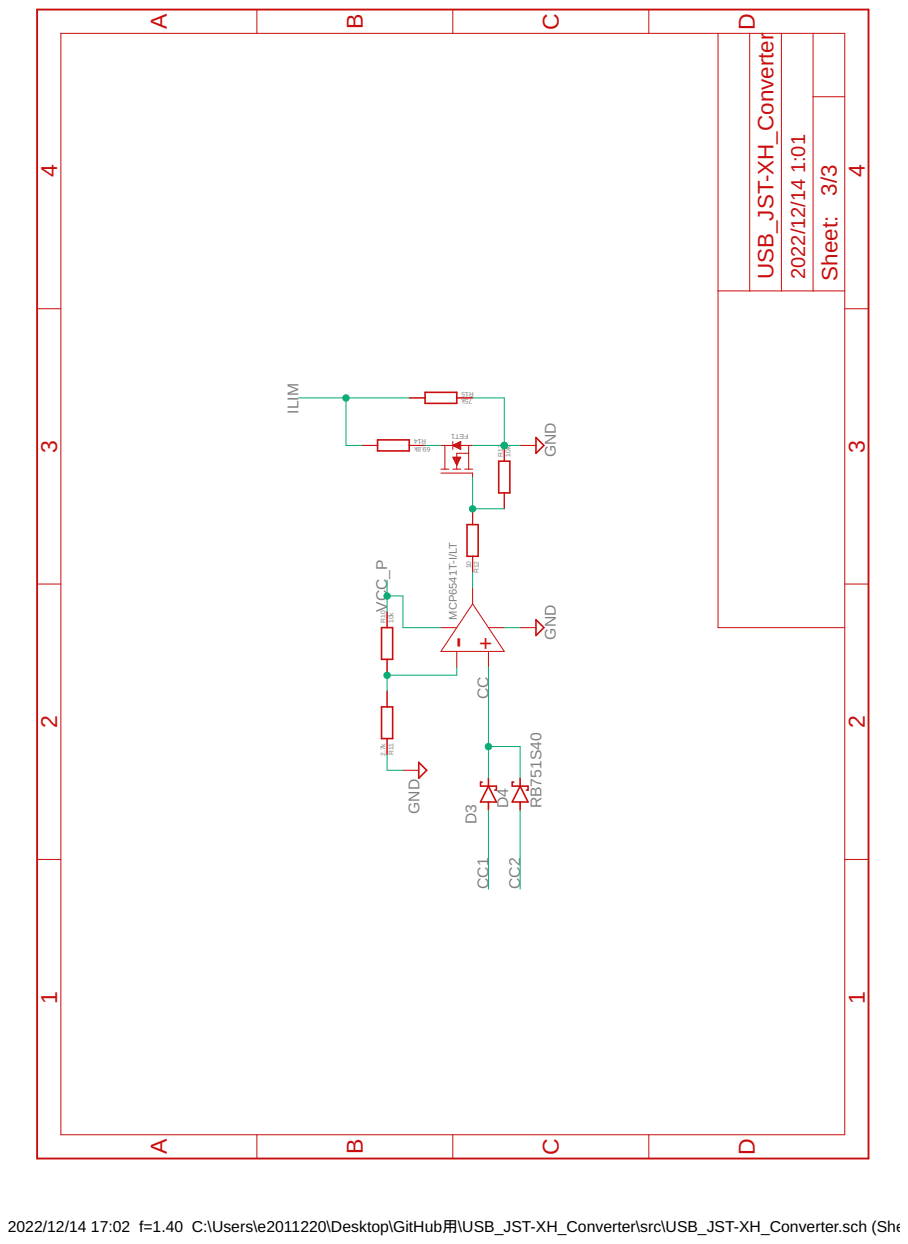
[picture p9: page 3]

2022/12/14 17:02 f=1.40 C:\Users\e2011220\Desktop\GitHub用\USB_JST-XH_Converter\src\USB_JST-XH_Converter.sch (Sheet: 3/3)

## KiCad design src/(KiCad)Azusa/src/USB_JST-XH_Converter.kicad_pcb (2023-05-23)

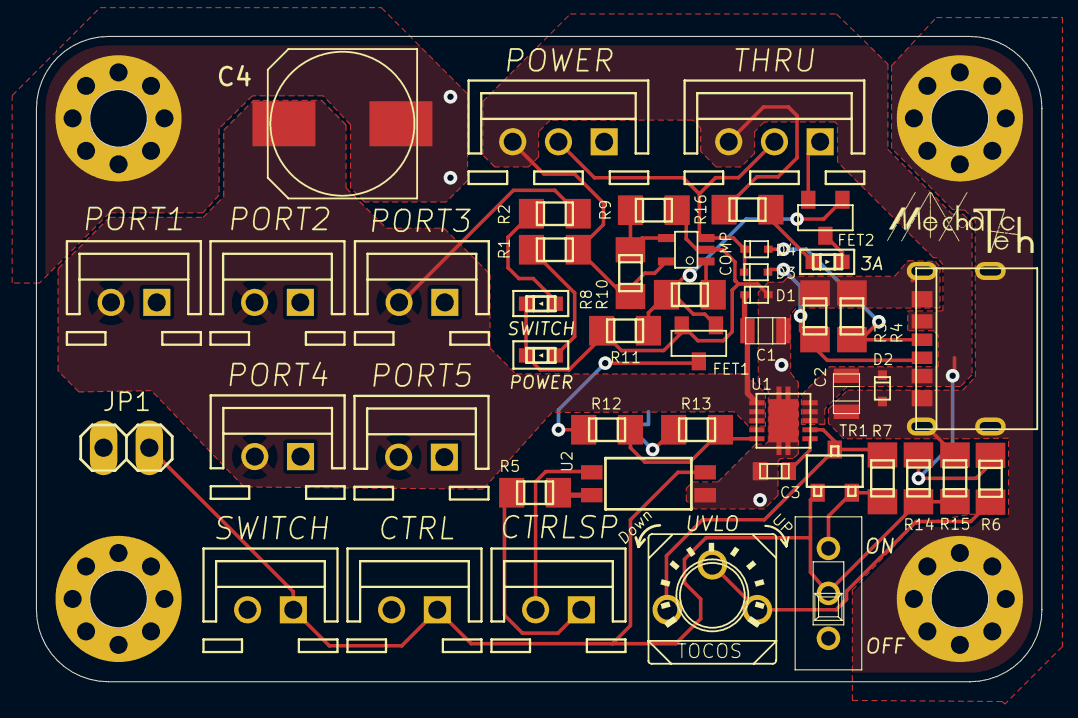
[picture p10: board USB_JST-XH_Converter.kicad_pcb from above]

Board: 2 copper layers, 55.9 x 35.9 mm, 51 parts (0 on the bottom side), 22 nets.

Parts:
C1, C2: GRM21BC72A105KE01
C3: GRM1885C1H242JA01D; GRM18
C4: UWT1E221MNL1GS
COMP1: MCP6541T-I_LT; SC-70-5
CTRL: 02-JST; B2B-XH
CTRLSP: 02-JST; B2B-XH
D1, D3, D4: RB751S40; SOD-523
D2: PJSD12TS; SOD-523
FET1, FET2: BSS138; SOT-23
H1, H2, H3, H4: MOUNT-HOLE3.2(NORESIST); 3,2
JP1: PINHD-1X2; 1X02
LED1: SML-E12V8WT86
PORT1, PORT2, PORT3, PORT4, PORT5: 02-JST; B2B-XH
POW1: SML-E12V8WT86
POWER: 03-JST; B3B-XH
R1, R2: RG2012N-101-B-T5; RG2012
R3, R4: 5.1k; RG2012
R5: 1k; RG2012
R6, R8, R13#2, R14: 10k; RG2012
R7: 3k; RG2012
R9: 2.7k; RG2012
R12: 69.8k; RG2012
R12#2: 10; RG2012
R13: 75k; RG2012
R16: 100k; RG2012
R18: 100; RG2012
SW1: SS-12D00G3
SW2: SML-E12V8WT86
SWITCH: 02-JST; B2B-XH
THRU: 03-JST; B3B-XH
TP1: GF063PB302K; GF063PB104K
TR1: 2SC3325
U1: TCKE805NAWSON10B_TOS-REC; WSON10B_TOS-RIC
U2: TLP293; SO4_TOS
USB1: UJC-HP-3-SMT-TR

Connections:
CC: COMP1.IN+, D3.C, D4.C, POWER.2, THRU.2
CC1: D3.A, R3.LEFT, USB1.A5
CC2: D4.A, R4.LEFT, USB1.B5
GND: C1.P$2, C2.P$2, C3.R, C4.C, COMP1.VSS, D1.A, D2.A, FET1.S, FET2.S, H1.P$1, H2.P$1, H3.P$1, H4.P$1, JP1.2, PORT1.1, PORT2.1, PORT3.1, PORT4.1, PORT5.1, POW1.K, POWER.1, R3.RIGHT, R4.RIGHT, R7.LEFT, R9.RIGHT, R13.RIGHT, R13#2.RIGHT, R16.RIGHT, SW1.R, SW2.K, SWITCH.2, THRU.1, TR1.E, U1.GND1, U1.GND2, U1.GND3, U1.GND4, U1.GND5, U2.3, USB1.A12, USB1.B12, USB1.SHIELD1, USB1.SHIELD2, USB1.SHIELD3, USB1.SHIELD4
ILIM: R12.LEFT, R13.LEFT, U1.ILIM
unnamed: C3.L, U1.DVDT
unnamed: COMP1.IN-, R8.LEFT, R9.LEFT
unnamed: COMP1.OUT, R12#2.RIGHT
unnamed: CTRLSP.1, R5.RIGHT
unnamed: CTRLSP.2, U2.1
unnamed: FET1.D, R12.RIGHT
unnamed: FET2.D, LED1.K
unnamed: LED1.A, R18.RIGHT
unnamed: POW1.A, R1.LEFT
unnamed: R2.LEFT, SW2.A
unnamed: R5.LEFT, U2.2
unnamed: R6.LEFT, TP1.CENTER, TP1.RIGHT
unnamed: R7.RIGHT, TP1.LEFT, TR1.C, U1.EN/UVLO
OUT: FET1.G, FET2.G, R12#2.LEFT, R13#2.LEFT
SWITCH: CTRL.1, JP1.1, R14.LEFT, R16.LEFT, SW1.C, SWITCH.1, TR1.B, U2.4
VCC: C1.P$1, C4.A, D1.C, PORT1.2, PORT2.2, PORT3.2, PORT4.2, PORT5.2, R2.RIGHT, U1.VOUT1, U1.VOUT2, U1.VOUT3
VCC_P: C2.P$1, COMP1.VDD, D2.C, POWER.3, R1.RIGHT, R6.RIGHT, R8.RIGHT, R14.RIGHT, R18.LEFT, THRU.3, U1.VIN1, U1.VIN2, U1.VIN3, USB1.A9, USB1.B9

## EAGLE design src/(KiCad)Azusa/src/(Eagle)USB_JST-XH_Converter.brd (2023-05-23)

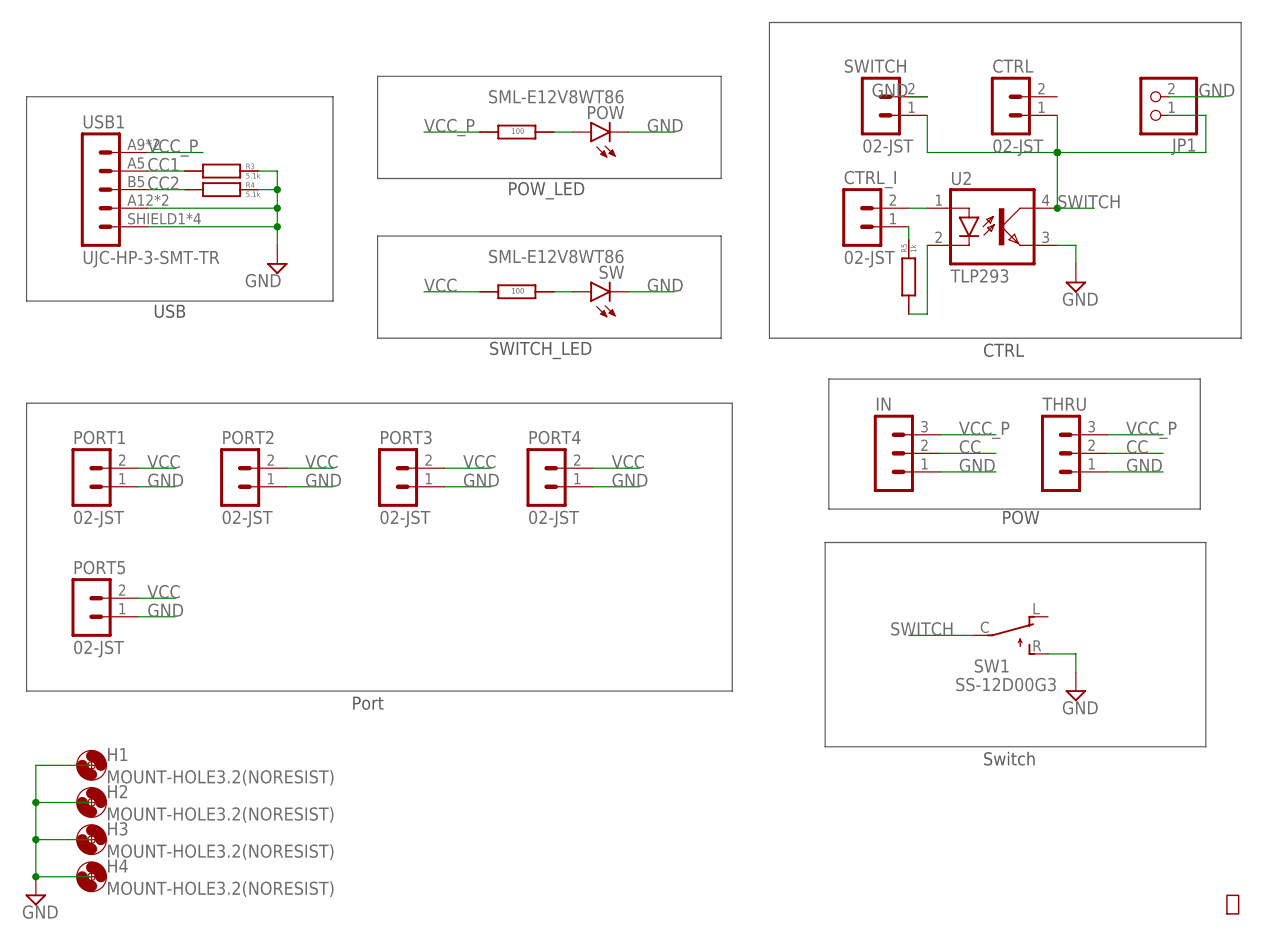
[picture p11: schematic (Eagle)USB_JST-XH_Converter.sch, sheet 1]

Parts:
CTRL: 02-JST; B2B-XH
CTRL_I: 02-JST; B2B-XH
H1, H2, H3, H4: MOUNT-HOLE3.2(NORESIST); 3,2
IN: 03-JST; B3B-XH
JP1: PINHD-1X2; 1X02
PORT1, PORT2, PORT3, PORT4, PORT5: 02-JST; B2B-XH
POW: SML-E12V8WT86
R1, R2: RG2012N-101-B-T5; RG2012
R3, R4: 5.1k; RG2012
R5: 1k; RG2012
SW: SML-E12V8WT86
SW1: SS-12D00G3
SWITCH: 02-JST; B2B-XH
THRU: 03-JST; B3B-XH
U2: TLP293; SO4_TOS
USB1: UJC-HP-3-SMT-TR

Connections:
CC: IN.2, THRU.2; also elsewhere on the board
CC1: R3.LEFT, USB1.A5 (CC1); also elsewhere on the board
CC2: R4.LEFT, USB1.B5 (CC2); also elsewhere on the board
GND: H1.P$1, H2.P$1, H3.P$1, H4.P$1, IN.1, JP1.2, PORT1.1, PORT2.1, PORT3.1, PORT4.1, PORT5.1, POW.K (C), R3.RIGHT, R4.RIGHT, SW.K (C), SW1.R, SWITCH.2, THRU.1, U2.3, USB1.A12 (GND), USB1.B12 (GND), USB1.SHIELD1 (SHIELD), USB1.SHIELD2 (SHIELD), USB1.SHIELD3 (SHIELD), USB1.SHIELD4 (SHIELD); also elsewhere on the board
unnamed: POW.A, R1.LEFT
unnamed: R2.LEFT, SW.A
unnamed: CTRL_I.2, U2.1
unnamed: CTRL_I.1, R5.RIGHT
unnamed: R5.LEFT, U2.2
SWITCH: CTRL.1, JP1.1, SW1.C, SWITCH.1, U2.4; also elsewhere on the board
VCC: PORT1.2, PORT2.2, PORT3.2, PORT4.2, PORT5.2, R2.RIGHT; also elsewhere on the board
VCC_P: IN.3, R1.RIGHT, THRU.3, USB1.A9 (V-BUS), USB1.B9 (V-BUS); also elsewhere on the board

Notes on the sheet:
Switch
Port
USB
SWITCH_LED
POW_LED
POW
CTRL

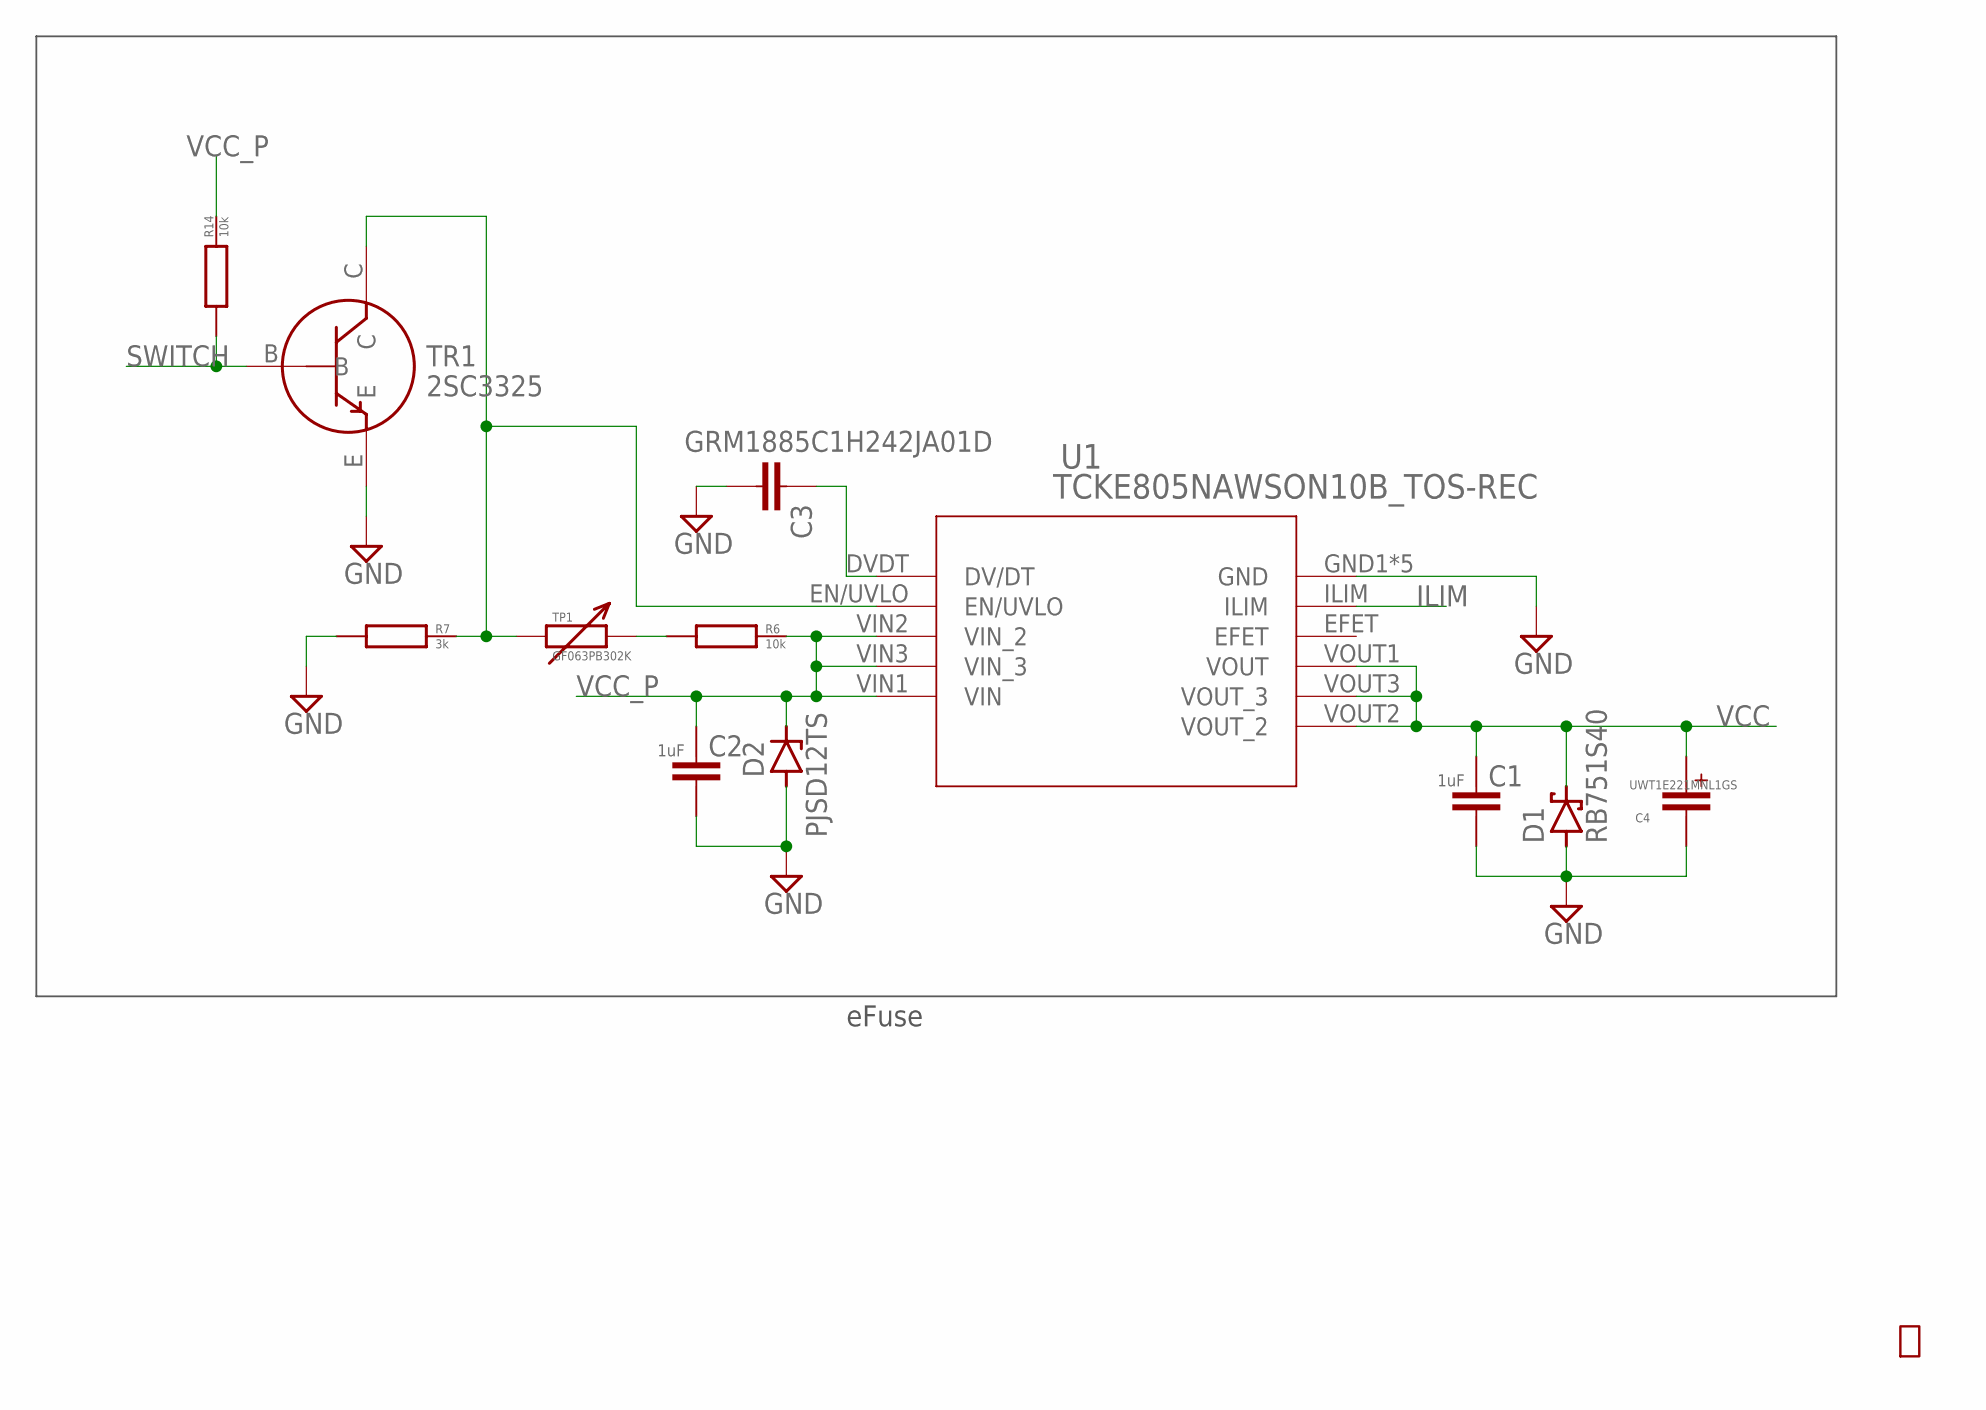
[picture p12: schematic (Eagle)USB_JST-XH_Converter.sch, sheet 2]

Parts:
C1, C2: GRM21BC72A105KE01
C3: GRM1885C1H242JA01D; GRM18
C4: UWT1E221MNL1GS
D1: RB751S40; SOD-523
D2: PJSD12TS; SOD-523
R6, R14: 10k; RG2012
R7: 3k; RG2012
TP1: GF063PB302K; GF063PB104K
TR1: 2SC3325
U1: TCKE805NAWSON10B_TOS-REC; WSON10B_TOS-RIC

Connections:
GND: C1.P$2, C2.P$2, C3.R (2), C4.C (CATHODE), D1.A, D2.A, R7.LEFT, TR1.E, U1.GND1 (GND), U1.GND2 (GND), U1.GND3 (GND), U1.GND4 (GND), U1.GND5 (GND); also elsewhere on the board
ILIM: U1.ILIM; also elsewhere on the board
unnamed: R7.RIGHT, TP1.LEFT, TR1.C, U1.EN/UVLO
unnamed: R6.LEFT, TP1.CENTER (RIGHT), TP1.RIGHT
unnamed: C3.L (1), U1.DVDT (DV/DT)
SWITCH: R14.LEFT, TR1.B; also elsewhere on the board
VCC: C1.P$1, C4.A (ANODE), D1.C, U1.VOUT1 (VOUT), U1.VOUT2 (VOUT_2), U1.VOUT3 (VOUT_3); also elsewhere on the board
VCC_P: C2.P$1, D2.C, R6.RIGHT, R14.RIGHT, U1.VIN1 (VIN), U1.VIN2 (VIN_2), U1.VIN3 (VIN_3); also elsewhere on the board

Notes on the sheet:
eFuse

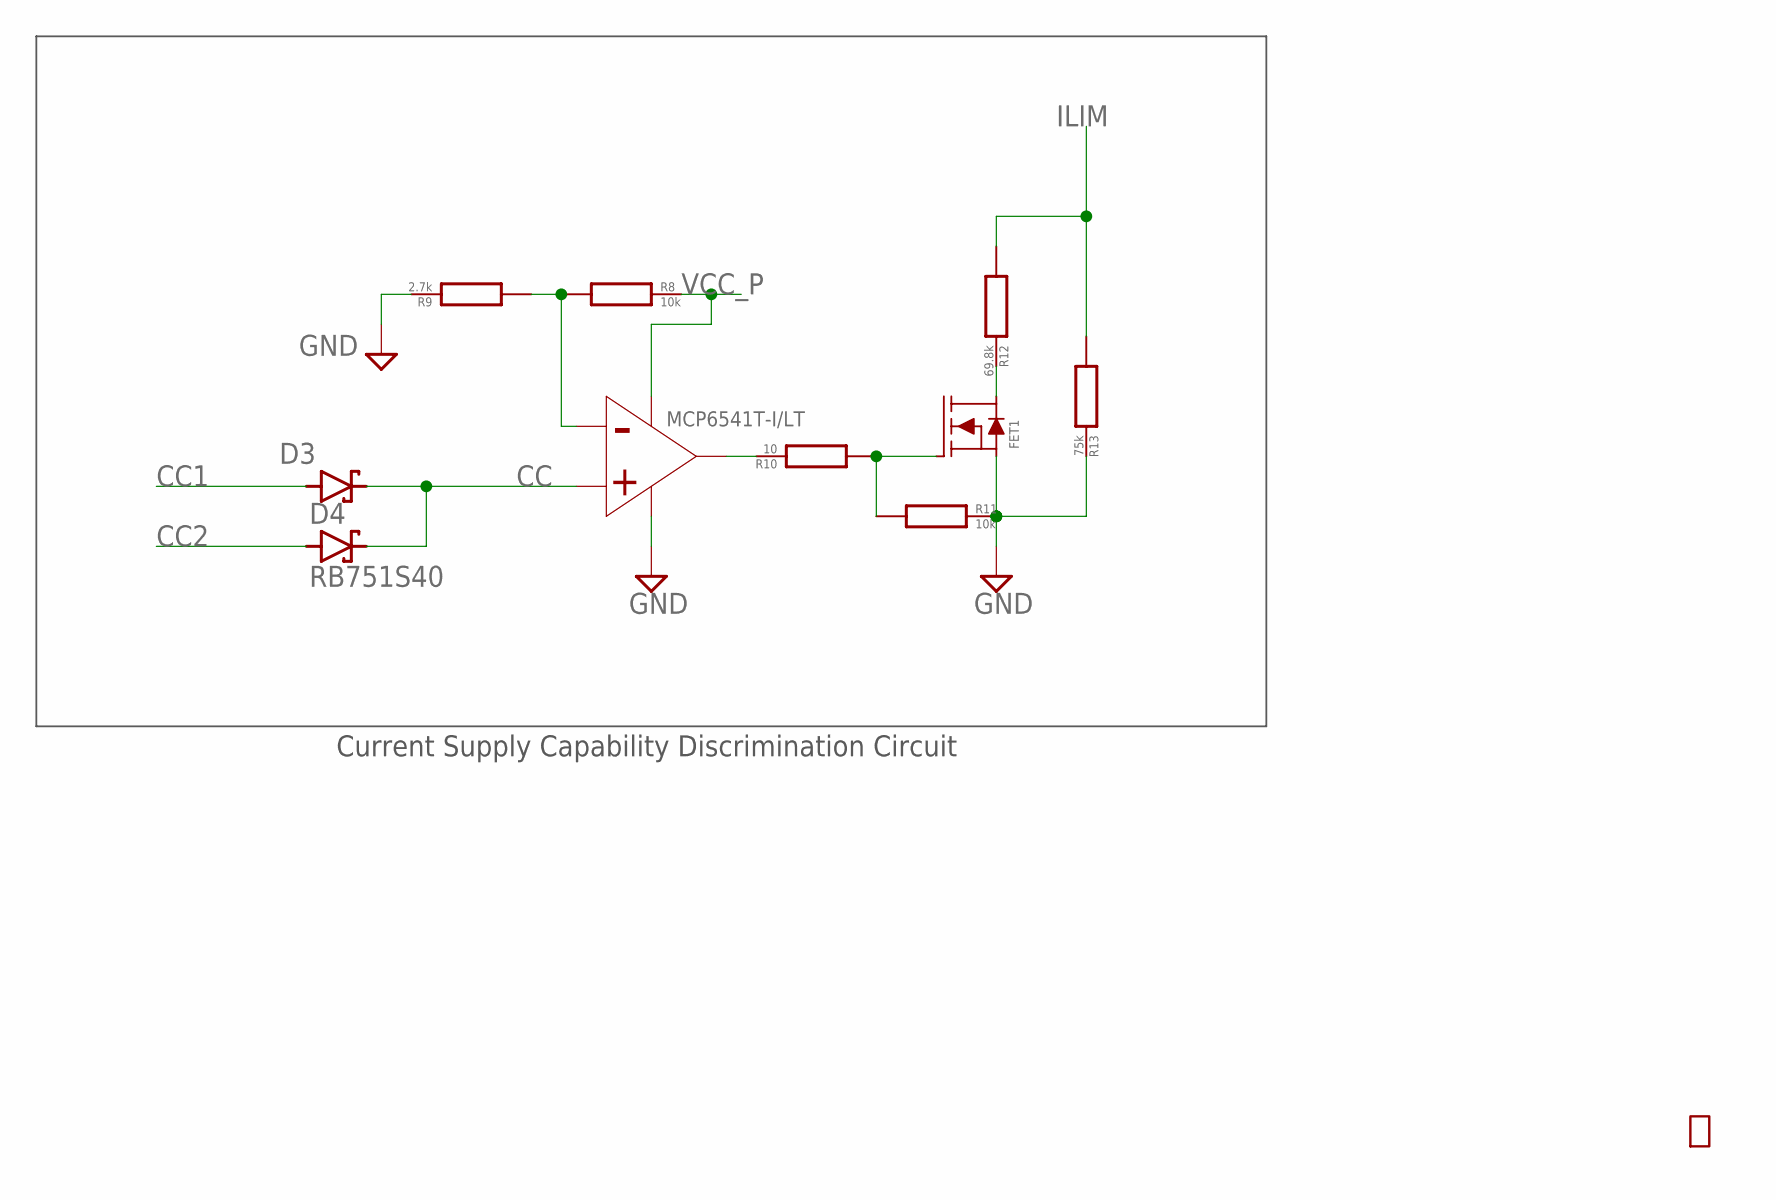
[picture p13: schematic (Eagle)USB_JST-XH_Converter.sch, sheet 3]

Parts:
COMP1: MCP6541T-I/LT; SC-70-5
D3, D4: RB751S40; SOD-523
FET1: BSS138; SOT-23
R8, R11: 10k; RG2012
R9: 2.7k; RG2012
R10: 10; RG2012
R12: 69.8k; RG2012
R13: 75k; RG2012

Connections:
CC: COMP1.IN+, D3.C, D4.C; also elsewhere on the board
CC1: D3.A; also elsewhere on the board
CC2: D4.A; also elsewhere on the board
GND: COMP1.VSS, FET1.S, R9.RIGHT, R11.RIGHT, R13.RIGHT; also elsewhere on the board
ILIM: R12.LEFT, R13.LEFT; also elsewhere on the board
unnamed: COMP1.IN-, R8.LEFT, R9.LEFT
unnamed: FET1.G, R10.LEFT, R11.LEFT
unnamed: COMP1.OUT, R10.RIGHT
unnamed: FET1.D, R12.RIGHT
VCC_P: COMP1.VDD, R8.RIGHT; also elsewhere on the board

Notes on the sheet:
Current Supply Capability Discrimination Circuit

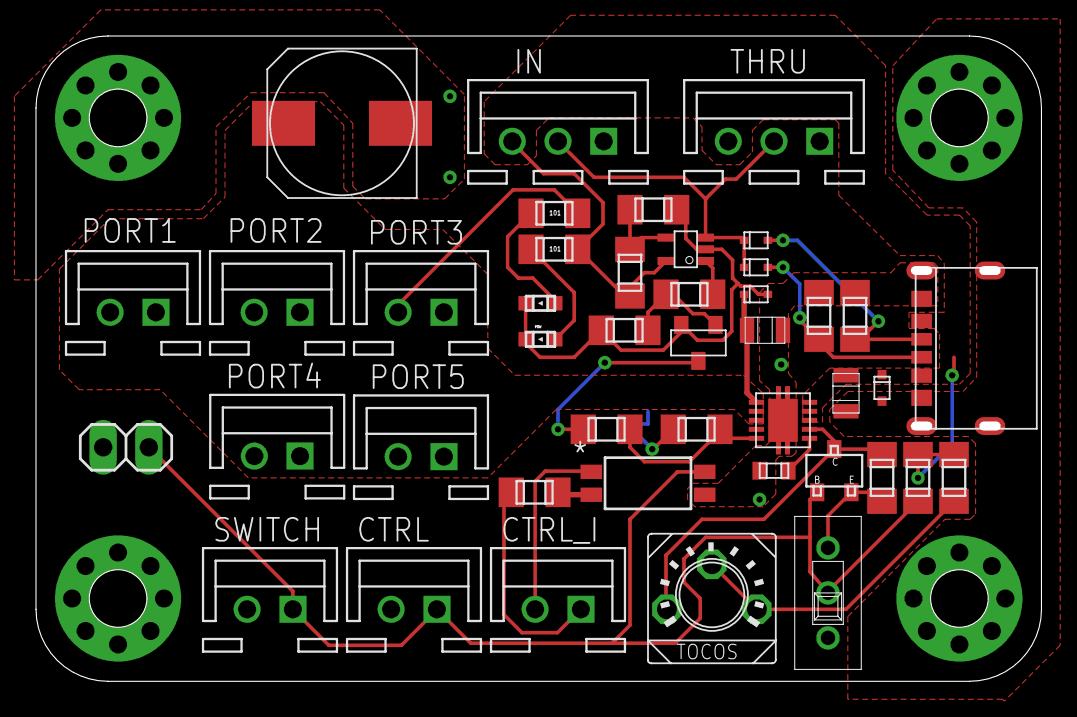
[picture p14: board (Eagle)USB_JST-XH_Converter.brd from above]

Board: 2 copper layers, 55.9 x 35.9 mm, 47 parts (0 on the bottom side), 20 nets.

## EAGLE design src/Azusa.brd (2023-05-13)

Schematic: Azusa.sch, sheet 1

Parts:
C2, C47, C50, C53, C56, C66, C67, C69, C71: GRM21BC72A105KE01
C3, C6, C8, C10, C11, C37, C38, C43, C46, C57, C60, C61, C64, C65, C70, C72, C73: GCM188L81H104KA57
C4, C5: GRM32ER71H106KA12
C7: A768EB566M1VLAE042
C9, C12: GRM32ER71E226KE15; 3225M
C39, C40, C41, C42, C44, C45, C48, C49, C51, C52, C54, C55, C58, C59, C62, C63: GRM1885C1H102JA01D; GRM18
C68: GRM0335C1H620GA01D; GRM0335C1E240GA01D
CON1, CON2, CON3, CON4: XT60PW-F
CON5: XT90PW-F
CTRL1, CTRL2: 02-JST; B2B-XH
D1, D2, D4: GS2M-LTP
D3: PJSD12TS; SOD-523
ECHO: PINHD-1X2; 1X02
EDGE1, EDGE2, EDGE3, EDGE4: 10046971-019LF-FEMAL; 10046971-019LF
FUSE1: FUSEHOLDER-3568
GND: PINHD-1X2; 1X02
H1, H2, H3, H4: MOUNT-HOLE3.2(NORESIST); 3,2
IN: XT90PW-M
INV_SW1, INV_SW2: 02-JST; B2B-XH
JP1, JP6, JP8, JP9, JP10: PINHD-1X3; 1X03
L1: 4.7uH; NRS5030T4R7MMGJ
LED1, LED2, LED3, LED8, LED9, LED10, LED11, LED12, LED13, LED14: SML-E12V8WT86
LED4: SMLE13BC8T; SML-E12V8WT86
NTC1: NCU15WB473F60RC
POW: 02-JST; B2B-XH
POW1: PINHD-1X2; 1X02
Q1, Q6, Q10: SQJA16EP-T1_GE3
Q2: SSM3J332R; SOT-23F
Q11, Q12: TMBT3906
R1, R67, R99, R104: 11.8k; CR0603
R2, R5, R79, R113, R116: 1.1k; CR0603
R3: 10; 0411V
R4: 560; CR0603
R6: 820; CR0603
R8, R9: 5.1k; CR0603
R10: 150Ω; CR0603
R12, R20, R21, R60, R65, R71, R115, R119, R121: 10k; CR0603
R18: 12k; CR0603
R19: 3k; CR0603
R22, R61, R66, R72: 20k; CR0603
R23, R24, R33, R58, R59, R62, R63, R64, R68, R69, R70, R73, R77, R120: 1k; CR0603
R32: 10; CR0603
R54, R95, R100, R105: 1.2k; CR0603
R55, R96, R101, R106: 15.8k; CR0603
R56, R97, R102, R107: 1.6k; CR0603
R57, R98, R103, R108: 3.3; CR0603
R74: 0; CR0603
R75: ∞; CR0603
R76: 56k; CR0603
R78, R85, R88: 100; CR0603
R80: 33k; CR0603
R81: 1.8k; CR0603
R82: 100k; CR0603
R83: 187k; CR0603
R84: 0Ω; CR0603
R86, R87, R89: 150; CR0603
R122: 300; CR0603
R123: 270; CR0603
SB1, SB2, SB3, SB4, SB8: RSX101VAM-30TR
SB5: V2P22LHM3/H
SB6: 1SS404,H3F
SW4, SW5: 2MS1-T2-B4-M2-Q-E-S
THRU1, THRU2: 02-JST; B2B-XH
TLP1, TLP3: TLP152
TP1, TP2, TP3, TP4, TP5, TP6, TP7, TP8: GF063PB103K; GF063PB104K
TR3: 2SC3325
U3: CH340E; MSOP-10
U4, U6, U8, U9: CZ-3A04; CZ3A07
U5: AP63205WU-7; AP63203WU-7
U7, U11, U12, U24, U27: MCP6541T-I/LT; SC-70-5
U10, U13, U17, U18, U21, U23, U25: TC7S14F
U14: TCK420G
U15: TCKE805NAWSON10B_TOS-REC; WSON10B_TOS-RIC
U16, U19, U26: TC7SH00FULJ; SSOP5-P-0.65A
U20: TLP293
U$4: AZ1117CH-3.3TRG1; AZ1117C
USB1: 5077CR-16SMC2-BK-TR
ZD1: MMSZ5231B-TP
ZD5: MMBZ5248B-TP

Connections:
5V1: C73.P$1, R121.RIGHT, R123.LEFT, U16.VCC, U17.VCC, U18.VCC, U19.VCC, U21.VCC, ZD1.CATHODE (C)
+3V3: C3.P$2, C11.P$1, C12.L (1), C37.P$2, C38.P$2, C57.P$2, C61.P$2, C72.P$1, EDGE1.P$27 (P27), EDGE2.P$27 (P27), EDGE3.P$27 (P27), EDGE4.P$27 (P27), R1.RIGHT, R21.LEFT, R24.RIGHT, R33.RIGHT, R55.RIGHT, R58.RIGHT, R59.RIGHT, R60.LEFT, R63.RIGHT, R64.RIGHT, R65.LEFT, R67.RIGHT, R69.RIGHT, R70.RIGHT, R71.LEFT, R80.LEFT, R82.LEFT, R88.RIGHT, R96.RIGHT, R99.RIGHT, R101.RIGHT, R104.RIGHT, R106.RIGHT, U3.3V3, U3.VCC, U4.VDD, U6.VDD, U7.VDD, U8.VDD, U9.VDD, U10.VCC, U11.VDD, U12.VDD, U13.VCC, U23.VCC, U24.VDD, U25.VCC, U26.VCC, U27.VDD, U$4.OUTPUT, U$4.VOUT (OUTPUT); also elsewhere on the board
+5V: C9.L (1), C10.P$1, Q2.S (SOURCE), Q11.E, R89.RIGHT, U$4.INPUT; also elsewhere on the board
CS1_OCD1: C44.L (1), JP8.3, R58.LEFT, U4.OCD1
CS1_OCD2: C45.L (1), JP8.1, R59.LEFT, U4.OCD2
CS1_REF1: C41.L (1), R1.LEFT, TP1.CENTER (LEFT), TP1.LEFT, U4.REF1
CS1_REF2: C42.L (1), R55.LEFT, TP2.CENTER (LEFT), TP2.LEFT, U4.REF2
CS2_OCD1: C48.L (1), JP1.3, R24.LEFT, U6.OCD1
CS2_OCD2: C49.L (1), JP1.1, R33.LEFT, U6.OCD2
CS2_REF1: C39.L (1), R67.LEFT, TP3.CENTER (LEFT), TP3.LEFT, U6.REF1
CS2_REF2: C40.L (1), R96.LEFT, TP4.CENTER (LEFT), TP4.LEFT, U6.REF2
CS3_OCD1: C51.L (1), JP9.3, R63.LEFT, U8.OCD1
CS3_OCD2: C52.L (1), JP9.1, R64.LEFT, U8.OCD2
CS3_REF1: C58.L (1), R99.LEFT, TP5.CENTER (LEFT), TP5.LEFT, U8.REF1
CS3_REF2: C59.L (1), R101.LEFT, TP6.CENTER (LEFT), TP6.LEFT, U8.REF2
CS4_OCD1: C54.L (1), JP10.3, R69.LEFT, U9.OCD1
CS4_OCD2: C55.L (1), JP10.1, R70.LEFT, U9.OCD2
CS4_REF1: C62.L (1), R104.LEFT, TP7.CENTER (LEFT), TP7.LEFT, U9.REF1
CS4_REF2: C63.L (1), R106.LEFT, TP8.CENTER (LEFT), TP8.LEFT, U9.REF2
CURRENT1: C43.P$2, R57.LEFT; also elsewhere on the board
CURRENT2: C46.P$2, R98.LEFT; also elsewhere on the board
CURRENT3: C60.P$2, R103.LEFT; also elsewhere on the board
CURRENT4: C64.P$2, R108.LEFT; also elsewhere on the board
DIR1: EDGE1.P$26 (P26); also elsewhere on the board
DIR2: EDGE2.P$26 (P26); also elsewhere on the board
DIR3: EDGE3.P$26 (P26); also elsewhere on the board
DIR4: EDGE4.P$26 (P26); also elsewhere on the board
E5V: C7.ANODE, JP6.3, L1.R, R86.RIGHT, U5.FB
EMERGENCY: R120.RIGHT, U14.VCT, U18.IN (I), U21.OUT (O)
IN1: EDGE1.P$6 (P6), EDGE1.P$7 (P7), EDGE1.P$8 (P8), EDGE1.P$9 (P9), EDGE1.P$10 (P10), EDGE1.P$11 (P11), EDGE1.P$40 (P40), EDGE1.P$41 (P41), EDGE1.P$42 (P42), EDGE1.P$43 (P43), EDGE1.P$44 (P44), U4.IN
IN2: EDGE2.P$6 (P6), EDGE2.P$7 (P7), EDGE2.P$8 (P8), EDGE2.P$9 (P9), EDGE2.P$10 (P10), EDGE2.P$11 (P11), EDGE2.P$40 (P40), EDGE2.P$41 (P41), EDGE2.P$42 (P42), EDGE2.P$43 (P43), EDGE2.P$44 (P44), U6.IN
IN3: EDGE3.P$6 (P6), EDGE3.P$7 (P7), EDGE3.P$8 (P8), EDGE3.P$9 (P9), EDGE3.P$10 (P10), EDGE3.P$11 (P11), EDGE3.P$40 (P40), EDGE3.P$41 (P41), EDGE3.P$42 (P42), EDGE3.P$43 (P43), EDGE3.P$44 (P44), U8.IN
IN4: EDGE4.P$6 (P6), EDGE4.P$7 (P7), EDGE4.P$8 (P8), EDGE4.P$9 (P9), EDGE4.P$10 (P10), EDGE4.P$11 (P11), EDGE4.P$40 (P40), EDGE4.P$41 (P41), EDGE4.P$42 (P42), EDGE4.P$43 (P43), EDGE4.P$44 (P44), U9.IN
IP1: CON1.-, U4.IP
IP2: CON2.-, U6.IP
IP3: CON3.-, U8.IP
IP4: CON4.-, U9.IP
unnamed: R57.RIGHT, U4.VOUT
unnamed: R56.RIGHT, TP2.RIGHT
unnamed: LED2.A, R5.RIGHT
unnamed: CON1.+, EDGE1.P$1 (P1), EDGE1.P$2 (P2), EDGE1.P$3 (P3), EDGE1.P$4 (P4), EDGE1.P$5 (P5), EDGE1.P$45 (P45), EDGE1.P$46 (P46), EDGE1.P$47 (P47), EDGE1.P$48 (P48), EDGE1.P$49 (P49), EDGE1.P$50 (P50)
unnamed: CON2.+, EDGE2.P$1 (P1), EDGE2.P$2 (P2), EDGE2.P$3 (P3), EDGE2.P$4 (P4), EDGE2.P$5 (P5), EDGE2.P$45 (P45), EDGE2.P$46 (P46), EDGE2.P$47 (P47), EDGE2.P$48 (P48), EDGE2.P$49 (P49), EDGE2.P$50 (P50)
unnamed: CON3.+, EDGE3.P$1 (P1), EDGE3.P$2 (P2), EDGE3.P$3 (P3), EDGE3.P$4 (P4), EDGE3.P$5 (P5), EDGE3.P$45 (P45), EDGE3.P$46 (P46), EDGE3.P$47 (P47), EDGE3.P$48 (P48), EDGE3.P$49 (P49), EDGE3.P$50 (P50)
unnamed: LED8.A, R116.RIGHT
unnamed: R74.LEFT, R75.RIGHT, U15.EN/UVLO
unnamed: JP8.2, U10.IN (I)
unnamed: CON4.+, EDGE4.P$1 (P1), EDGE4.P$2 (P2), EDGE4.P$3 (P3), EDGE4.P$4 (P4), EDGE4.P$5 (P5), EDGE4.P$45 (P45), EDGE4.P$46 (P46), EDGE4.P$47 (P47), EDGE4.P$48 (P48), EDGE4.P$49 (P49), EDGE4.P$50 (P50)
unnamed: Q10.D, R3.1
unnamed: R77.LEFT, TLP1.VO (VOUT)
unnamed: R54.RIGHT, TP1.RIGHT
unnamed: R77.RIGHT, R115.RIGHT, TR3.B
unnamed: LED8.K (C), TR3.C, U20.CATHODE
unnamed: LED1.A, R2.RIGHT
unnamed: R60.RIGHT, R61.LEFT, U11.IN-
unnamed: INV_SW1.2, INV_SW2.1, SW4.O, SW5.P
unnamed: C67.P$1, D3.C, JP6.2, R74.RIGHT, U15.VIN1 (VIN), U15.VIN2 (VIN_2), U15.VIN3 (VIN_3)
unnamed: CTRL1.1, CTRL2.1, INV_SW1.1, LED3.K (C), R115.LEFT, SW4.P, THRU1.1, THRU2.1, TR3.E
unnamed: U16.INB (I1), U17.OUT (O)
unnamed: LED3.A, R113.RIGHT
unnamed: FUSE1.R1 (R), FUSE1.R2 (R), IN.+, R79.LEFT
unnamed: Q1.G, Q6.G, U14.VGATE2
unnamed: R8.RIGHT, USB1.CC2
unnamed: R9.RIGHT, USB1.CC1
unnamed: U3.UD+, USB1.DP1, USB1.DP2
unnamed: U3.UD-, USB1.DN1, USB1.DN2
unnamed: R10.RIGHT, U3.TNOW
unnamed: LED4.A, R10.LEFT
unnamed: D1.A, POW1.2
unnamed: R18.LEFT, R19.RIGHT, U5.EN
unnamed: D2.A, POW.2
unnamed: C6.P$2, L1.L, U5.SW
unnamed: C6.P$1, U5.BST
unnamed: R21.RIGHT, R22.LEFT, U7.IN-
unnamed: Q11.B, Q12.B, Q12.C, R12.RIGHT
unnamed: LED12.A, R87.LEFT
unnamed: C69.P$1, Q2.D (DRAIN), Q12.E, SB6.C, U15.VOUT1 (VOUT), U15.VOUT2 (VOUT_2), U15.VOUT3 (VOUT_3)
unnamed: C50.P$1, R62.LEFT, U11.IN+
unnamed: SB2.A, U11.OUT
unnamed: C47.P$1, R23.LEFT, U7.IN+
unnamed: R95.RIGHT, TP3.RIGHT
unnamed: R97.RIGHT, TP4.RIGHT
unnamed: R98.RIGHT, U6.VOUT
unnamed: R100.RIGHT, TP5.RIGHT
unnamed: JP1.2, U23.IN (I)
unnamed: R65.RIGHT, R66.LEFT, U12.IN-
unnamed: C53.P$1, R68.LEFT, U12.IN+
unnamed: SB3.A, U12.OUT
unnamed: JP9.2, U13.IN (I)
unnamed: R68.RIGHT, U13.OUT (O)
unnamed: R71.RIGHT, R72.LEFT, U24.IN-
unnamed: C56.P$1, R73.LEFT, U24.IN+
unnamed: SB4.A, U24.OUT
unnamed: R78.LEFT, U26.OUT (O)
unnamed: C71.P$1, R120.LEFT, U17.IN (I)
unnamed: R4.RIGHT, U20.ANODE
unnamed: D4.C, R6.LEFT, TLP3.VO (VOUT)
unnamed: Q10.G, R6.RIGHT, R32.RIGHT, R119.RIGHT, ZD5.CATHODE (C)
unnamed: SB1.A, U7.OUT
unnamed: R102.RIGHT, TP6.RIGHT
unnamed: R103.RIGHT, U8.VOUT
unnamed: R105.RIGHT, TP7.RIGHT
unnamed: R107.RIGHT, TP8.RIGHT
unnamed: R108.RIGHT, U9.VOUT
unnamed: Q2.G (GATE), Q11.C, R20.RIGHT
unnamed: R23.RIGHT, U10.OUT (O)
unnamed: R122.LEFT, U19.OUT (O)
unnamed: U16.INA (I0), U18.OUT (O)
unnamed: U16.OUT (O), U19.INA (I0), U19.INB (I1)
unnamed: R121.LEFT, U20.COLLECTOR, U21.IN (I)
unnamed: R122.RIGHT, TLP3.ANODE
unnamed: C66.P$1, EDGE1.P$12 (P12), EDGE1.P$13 (P13), EDGE1.P$14 (P14), EDGE1.P$15 (P15), EDGE1.P$16 (P16), EDGE1.P$17 (P17), EDGE1.P$18 (P18), EDGE1.P$19 (P19), EDGE1.P$20 (P20), EDGE1.P$21 (P21), EDGE1.P$22 (P22), EDGE1.P$23 (P23), EDGE2.P$12 (P12), EDGE2.P$13 (P13), EDGE2.P$14 (P14), EDGE2.P$15 (P15), EDGE2.P$16 (P16), EDGE2.P$17 (P17), EDGE2.P$18 (P18), EDGE2.P$19 (P19), EDGE2.P$20 (P20), EDGE2.P$21 (P21), EDGE2.P$22 (P22), EDGE2.P$23 (P23), EDGE3.P$12 (P12), EDGE3.P$13 (P13), EDGE3.P$14 (P14), EDGE3.P$15 (P15), EDGE3.P$16 (P16), EDGE3.P$17 (P17), EDGE3.P$18 (P18), EDGE3.P$19 (P19), EDGE3.P$20 (P20), EDGE3.P$21 (P21), EDGE3.P$22 (P22), EDGE3.P$23 (P23), EDGE4.P$12 (P12), EDGE4.P$13 (P13), EDGE4.P$14 (P14), EDGE4.P$15 (P15), EDGE4.P$16 (P16), EDGE4.P$17 (P17), EDGE4.P$18 (P18), EDGE4.P$19 (P19), EDGE4.P$20 (P20), EDGE4.P$21 (P21), EDGE4.P$22 (P22), EDGE4.P$23 (P23), Q1.S1 (S), Q1.S2 (S), Q1.S3 (S), Q6.S1 (S), Q6.S2 (S), Q6.S3 (S), R3.2, R5.LEFT, SB5.A, U14.VOUT
unnamed: D4.A, R32.LEFT
unnamed: R62.RIGHT, U23.OUT (O)
unnamed: JP10.2, U25.IN (I)
unnamed: R73.RIGHT, U25.OUT (O)
unnamed: R76.RIGHT, U15.ILIM
unnamed: C68.1, U15.DVDT (DV/DT)
unnamed: R78.RIGHT, TLP1.ANODE
unnamed: LED9.A, R79.RIGHT
unnamed: R84.RIGHT, U3.RTS#
unnamed: R80.RIGHT, R81.LEFT, R83.LEFT, U27.IN+
unnamed: R84.LEFT, U3.CTS#
unnamed: LED10.A, R85.RIGHT
unnamed: LED11.A, R86.LEFT
unnamed: R83.RIGHT, R85.LEFT, SB8.A, U27.OUT
unnamed: LED13.A, R89.LEFT
unnamed: LED14.A, R88.LEFT
PGND: C2.P$2, C65.P$2, C66.P$2, C70.P$2, C71.P$2, C73.P$2, CON5.-, EDGE1.P$28 (P28), EDGE1.P$29 (P29), EDGE1.P$30 (P30), EDGE1.P$31 (P31), EDGE1.P$32 (P32), EDGE1.P$33 (P33), EDGE1.P$34 (P34), EDGE1.P$35 (P35), EDGE1.P$36 (P36), EDGE1.P$37 (P37), EDGE1.P$38 (P38), EDGE1.P$39 (P39), EDGE2.P$28 (P28), EDGE2.P$29 (P29), EDGE2.P$30 (P30), EDGE2.P$31 (P31), EDGE2.P$32 (P32), EDGE2.P$33 (P33), EDGE2.P$34 (P34), EDGE2.P$35 (P35), EDGE2.P$36 (P36), EDGE2.P$37 (P37), EDGE2.P$38 (P38), EDGE2.P$39 (P39), EDGE3.P$28 (P28), EDGE3.P$29 (P29), EDGE3.P$30 (P30), EDGE3.P$31 (P31), EDGE3.P$32 (P32), EDGE3.P$33 (P33), EDGE3.P$34 (P34), EDGE3.P$35 (P35), EDGE3.P$36 (P36), EDGE3.P$37 (P37), EDGE3.P$38 (P38), EDGE3.P$39 (P39), EDGE4.P$28 (P28), EDGE4.P$29 (P29), EDGE4.P$30 (P30), EDGE4.P$31 (P31), EDGE4.P$32 (P32), EDGE4.P$33 (P33), EDGE4.P$34 (P34), EDGE4.P$35 (P35), EDGE4.P$36 (P36), EDGE4.P$37 (P37), EDGE4.P$38 (P38), EDGE4.P$39 (P39), GND.2, H1.P$1, H2.P$1, IN.-, INV_SW2.2, LED1.K (C), LED2.K (C), LED9.K (C), Q10.S1 (S), Q10.S2 (S), Q10.S3 (S), R119.LEFT, SW5.O, TLP1.GND, TLP3.CATHODE, TLP3.GND, U14.GND, U16.GND, U17.GND, U18.GND, U19.GND, U20.EMITTER, U21.GND, ZD1.ANODE (A), ZD5.ANODE (A)
PWM1: EDGE1.P$25 (P25); also elsewhere on the board
PWM2: EDGE2.P$25 (P25); also elsewhere on the board
PWM3: EDGE3.P$25 (P25); also elsewhere on the board
PWM4: EDGE4.P$25 (P25); also elsewhere on the board
SGND: C3.P$1, C4.R, C5.R, C7.CATHODE, C8.P$2, C9.R (2), C10.P$2, C11.P$2, C12.R (2), C37.P$1, C38.P$1, C39.R (2), C40.R (2), C41.R (2), C42.R (2), C43.P$1, C44.R (2), C45.R (2), C46.P$1, C47.P$2, C48.R (2), C49.R (2), C50.P$2, C51.R (2), C52.R (2), C53.P$2, C54.R (2), C55.R (2), C56.P$2, C57.P$1, C58.R (2), C59.R (2), C60.P$1, C61.P$1, C62.R (2), C63.R (2), C64.P$1, C67.P$2, C68.2, C69.P$2, C72.P$2, D3.A, EDGE1.P$24 (P24), EDGE2.P$24 (P24), EDGE3.P$24 (P24), EDGE4.P$24 (P24), GND.1, H3.P$1, H4.P$1, LED4.K (C), LED10.K (C), LED11.K (C), LED12.K (C), LED13.K (C), LED14.K (C), NTC1.L (1), POW.1, R8.LEFT, R9.LEFT, R12.LEFT, R19.LEFT, R20.LEFT, R22.RIGHT, R54.LEFT, R56.LEFT, R61.RIGHT, R66.RIGHT, R72.RIGHT, R75.LEFT, R76.LEFT, R81.RIGHT, R95.LEFT, R97.LEFT, R100.LEFT, R102.LEFT, R105.LEFT, R107.LEFT, SB6.A, TLP1.CATHODE, U3.GND, U4.VSS1, U4.VSS2, U5.GND, U6.VSS1, U6.VSS2, U7.VSS, U8.VSS1, U8.VSS2, U9.VSS1, U9.VSS2, U10.GND, U11.VSS, U12.VSS, U13.GND, U15.GND1 (GND), U15.GND2 (GND), U15.GND3 (GND), U15.GND4 (GND), U15.GND5 (GND), U23.GND, U24.VSS, U25.GND, U26.GND, U27.VSS, U$4.GND, USB1.GND1 (GND), USB1.GND2 (GND), USB1.SHIELD1 (SHIELD), USB1.SHIELD2 (SHIELD), USB1.SHIELD3 (SHIELD), USB1.SHIELD4 (SHIELD); also elsewhere on the board
SHUTDOWN: SB1.C, SB2.C, SB3.C, SB4.C, SB8.C, U26.INA (I0), U26.INB (I1); also elsewhere on the board
THERMAL: NTC1.R (2), R82.RIGHT, U27.IN-; also elsewhere on the board
U5V: JP6.1, R87.RIGHT, USB1.VBUS1 (VBUS), USB1.VBUS2 (VBUS)
USART_RX: ECHO.1, U3.TXD; also elsewhere on the board
USART_TX: ECHO.2, U3.RXD; also elsewhere on the board
V+: C4.L, C5.L, C8.P$1, D1.C, D2.C, R18.RIGHT, U5.VIN
VCC: C2.P$1, C65.P$1, C70.P$1, CON5.+, CTRL1.2, CTRL2.2, FUSE1.L1 (L), FUSE1.L2 (L), POW1.1, Q1.D, Q6.D, R2.LEFT, R4.LEFT, R113.LEFT, R116.LEFT, R123.RIGHT, SB5.C, THRU1.2, THRU2.2, TLP1.VCC, TLP3.VCC, U14.VIN

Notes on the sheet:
Battery
Control
Output
DeadTime:0.606ms(approximately)
OCD TIMER
Current Sensor
USB2.0(Type C)
Power Management
GND_COM
OTP
23.368℃/W
Continuous Max:92[A]

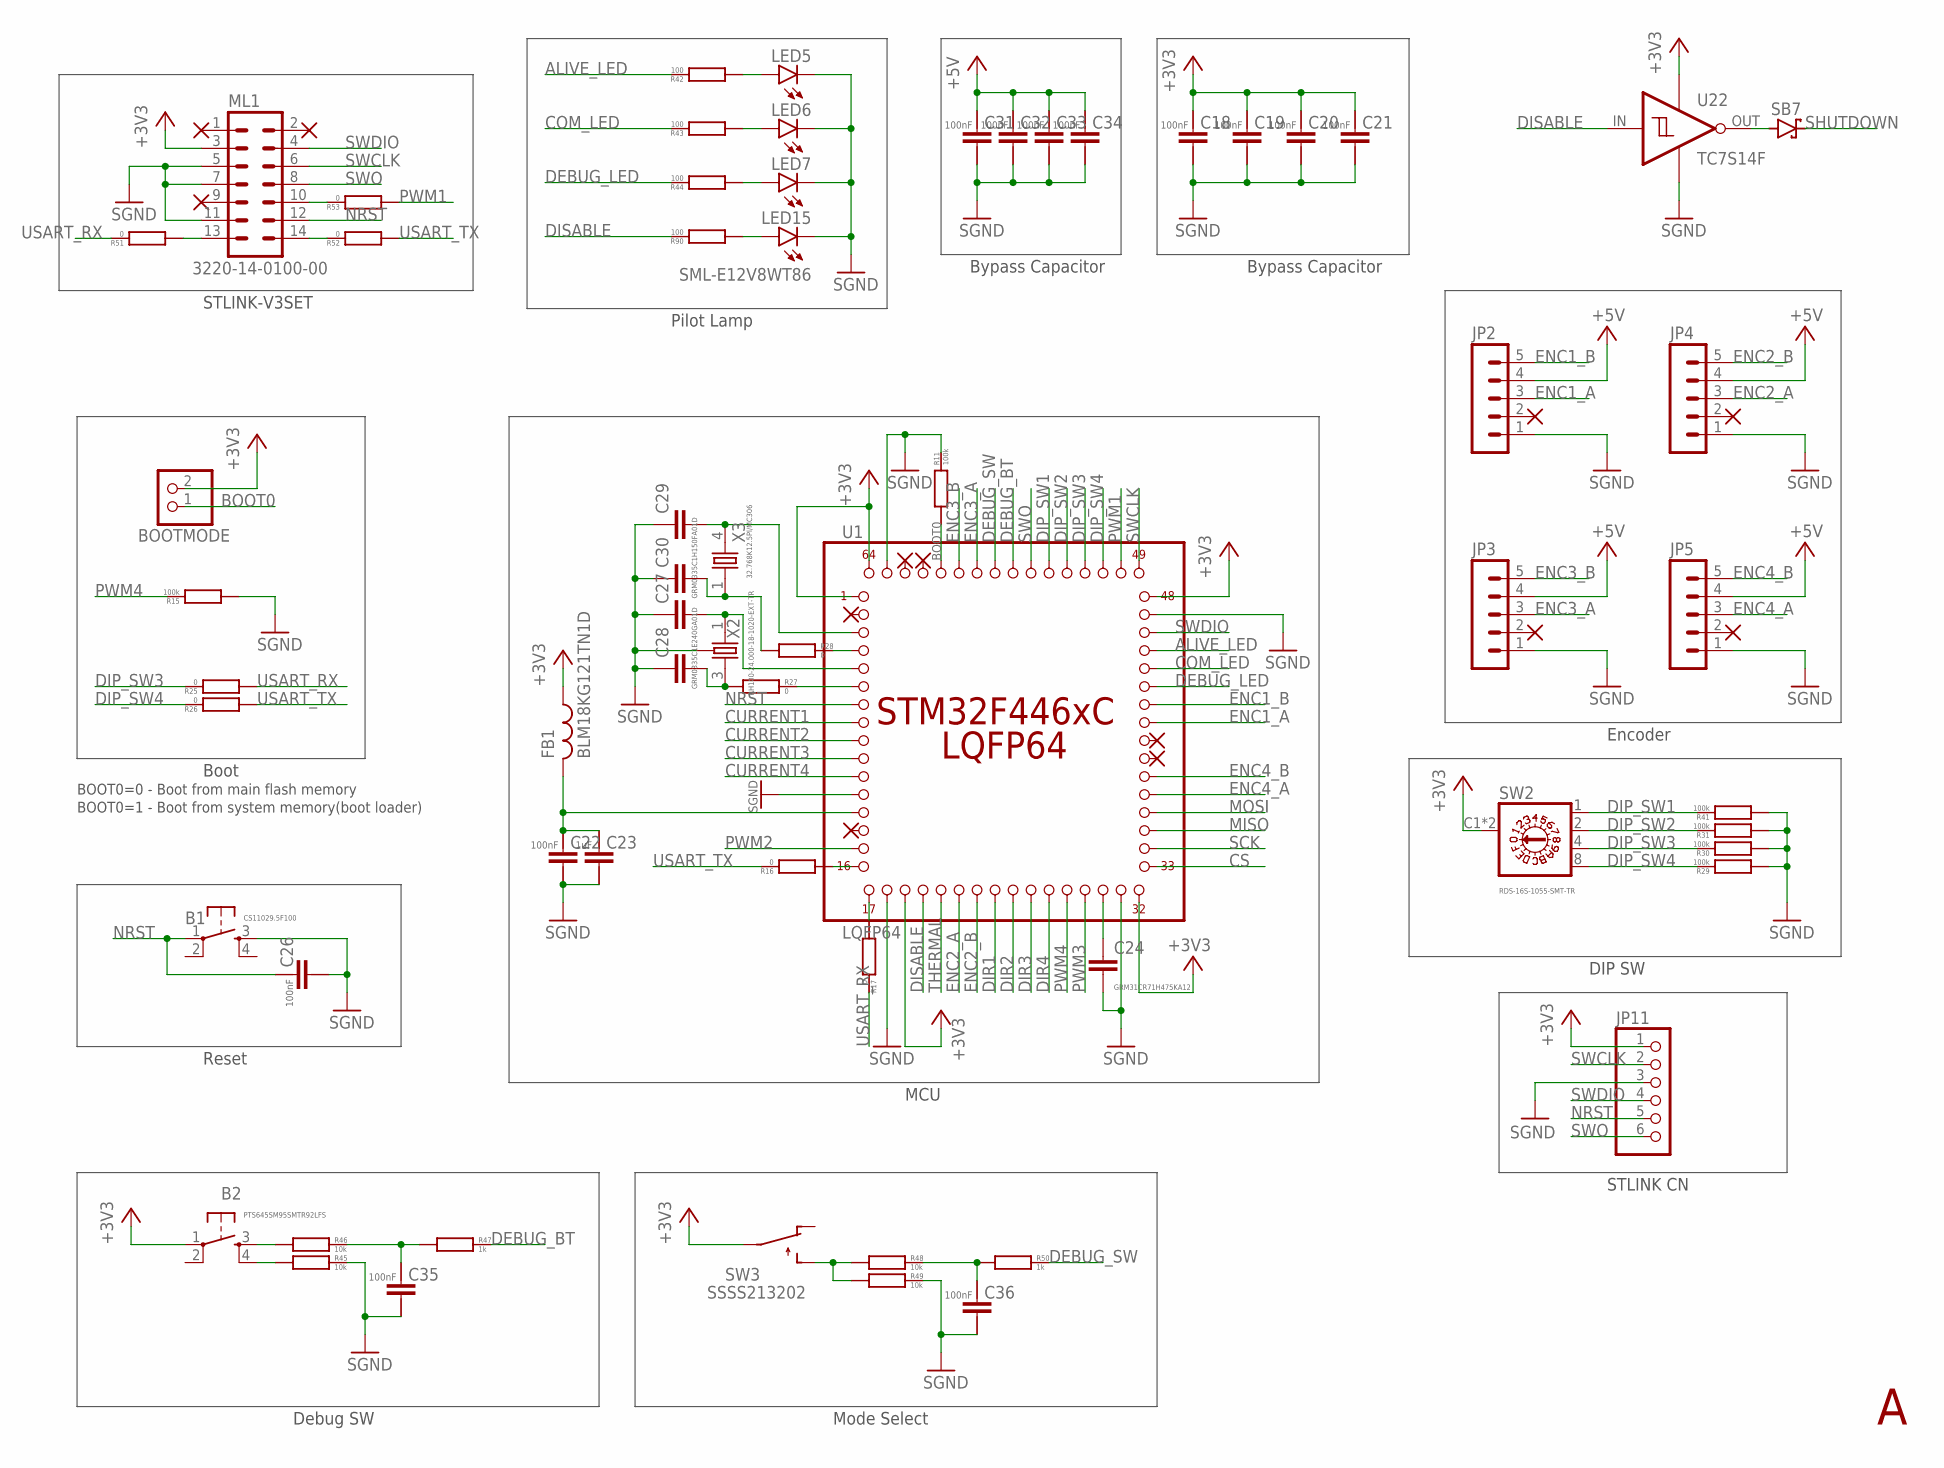
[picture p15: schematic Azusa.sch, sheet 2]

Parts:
B1: CS11029.5F100
B2: PTS645SM95SMTR92LFS
BOOTMODE: PINHD-1X2; 1X02
C18, C19, C20, C21, C22, C26, C31, C32, C33, C34, C35, C36: GCM188L81H104KA57
C23: GRM21BC72A105KE01
C24: GRM31CR71H475KA12
C27, C28: GRM0335C1E240GA01D
C29, C30: GRM0335C1H150FA01D; GRM0335C1H120GA01
FB1: BLM18KG121TN1D
JP2, JP3, JP4, JP5: 05-JST; B5B-XH
JP11: PINHD-1X6; 1X06
LED5, LED6, LED7, LED15: SML-E12V8WT86
ML1: 3220-14-0100-00
R11, R15, R29, R30, R31, R41: 100k; CR0603
R16, R17, R25, R26, R27, R28, R51, R52, R53: 0; CR0603
R42, R43, R44, R90: 100; CR0603
R45, R46, R48, R49: 10k; CR0603
R47, R50: 1k; CR0603
SB7: RSX101VAM-30TR
SW2: RDS-16S-1055-SMT-TR
SW3: SSSS213202
U1: LQFP64; STM32F446XC
U22: TC7S14F
X2: RH100-24.000-18-1020-EXT-TR
X3: 32.768K12.5PI/MC306

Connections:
+3V3: B2.1, BOOTMODE.2, C18.P$1, C19.P$1, C20.P$1, C21.P$1, FB1.1, JP11.1, ML1.3, SW2.C1 (C), SW2.C2 (C), SW3.2A (C), SW3.2B (C), U1.P1, U1.P19, U1.P32, U1.P48, U1.P64, U22.VCC; also elsewhere on the board
+5V: C31.P$1, C32.P$1, C33.P$1, C34.P$1, JP2.4, JP3.4, JP4.4, JP5.4; also elsewhere on the board
ALIVE_LED: R42.RIGHT, U1.P45
BOOT0: BOOTMODE.1, R11.LEFT, U1.P60
COM_LED: R43.RIGHT, U1.P44; also elsewhere on the board
CS: U1.P33; also elsewhere on the board
CURRENT1: U1.P8; also elsewhere on the board
CURRENT2: U1.P9; also elsewhere on the board
CURRENT3: U1.P10; also elsewhere on the board
CURRENT4: U1.P11; also elsewhere on the board
DEBUG_BT: R47.RIGHT, U1.P56
DEBUG_LED: R44.RIGHT, U1.P43
DEBUG_SW: R50.RIGHT, U1.P57
DIP_SW1: R41.RIGHT, SW2.1, U1.P54
DIP_SW2: R31.RIGHT, SW2.2, U1.P53
DIP_SW3: R25.RIGHT, R30.RIGHT, SW2.4, U1.P52
DIP_SW4: R26.RIGHT, R29.RIGHT, SW2.8, U1.P51
DIR1: U1.P24; also elsewhere on the board
DIR2: U1.P25; also elsewhere on the board
DIR3: U1.P26; also elsewhere on the board
DIR4: U1.P27; also elsewhere on the board
DISABLE: R90.RIGHT, U1.P20, U22.IN (I)
ENC1_A: JP2.3, U1.P41
ENC1_B: JP2.5, U1.P42
ENC2_A: JP4.3, U1.P22
ENC2_B: JP4.5, U1.P23
ENC3_A: JP3.3, U1.P58
ENC3_B: JP3.5, U1.P59
ENC4_A: JP5.3, U1.P37
ENC4_B: JP5.5, U1.P38
MISO: U1.P35; also elsewhere on the board
MOSI: U1.P36; also elsewhere on the board
unnamed: R16.LEFT, U1.P16
unnamed: R17.LEFT, U1.P17
unnamed: C22.P$1, C23.P$1, FB1.2, U1.P13
unnamed: C24.1, U1.P30
unnamed: C27.2, U1.P5, X2.1
unnamed: R28.RIGHT, U1.P4
unnamed: R27.RIGHT, U1.P6
unnamed: C28.2, R27.LEFT, X2.3 (2)
unnamed: C30.2, R28.LEFT, X3.1
unnamed: C29.2, U1.P3, X3.4 (2)
unnamed: LED5.A, R42.LEFT
unnamed: LED6.A, R43.LEFT
unnamed: LED7.A, R44.LEFT
unnamed: B2.4, R45.LEFT
unnamed: B2.3, R46.LEFT
unnamed: R48.LEFT, R49.LEFT, SW3.3A (R), SW3.3B (R)
unnamed: ML1.13, R51.LEFT
unnamed: C36.P$1, R48.RIGHT, R50.LEFT
unnamed: ML1.14, R52.RIGHT
unnamed: ML1.10, R53.RIGHT
unnamed: C35.P$1, R46.RIGHT, R47.LEFT
unnamed: SB7.A, U22.OUT (O)
unnamed: LED15.A, R90.LEFT
NRST: B1.1, C26.P$1, JP11.5, ML1.12, U1.P7
PWM1: R53.LEFT, U1.P50; also elsewhere on the board
PWM2: U1.P15; also elsewhere on the board
PWM3: U1.P29; also elsewhere on the board
PWM4: R15.RIGHT, U1.P28; also elsewhere on the board
SCK: U1.P34; also elsewhere on the board
SGND: B1.3, C18.P$2, C19.P$2, C20.P$2, C21.P$2, C22.P$2, C23.P$2, C24.2, C26.P$2, C27.1, C28.1, C29.1, C30.1, C31.P$2, C32.P$2, C33.P$2, C34.P$2, C35.P$2, C36.P$2, JP2.1, JP3.1, JP4.1, JP5.1, JP11.3, LED5.K (C), LED6.K (C), LED7.K (C), LED15.K (C), ML1.5, ML1.7, ML1.11, R11.RIGHT, R15.LEFT, R29.LEFT, R30.LEFT, R31.LEFT, R41.LEFT, R45.RIGHT, R49.RIGHT, U1.P12, U1.P18, U1.P31, U1.P47, U1.P63, U22.GND, X2.2 (SHIELD), X2.4 (SHIELD); also elsewhere on the board
SHUTDOWN: SB7.C; also elsewhere on the board
SWCLK: JP11.2, ML1.6, U1.P49
SWDIO: JP11.4, ML1.4, U1.P46
SWO: JP11.6, ML1.8, U1.P55
THERMAL: U1.P21; also elsewhere on the board
USART_RX: R17.RIGHT, R25.LEFT, R51.RIGHT; also elsewhere on the board
USART_TX: R16.RIGHT, R26.LEFT, R52.LEFT; also elsewhere on the board

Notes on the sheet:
BOOT0=0 - Boot from main flash memory
Boot
BOOT0=1 - Boot from system memory(boot loader)
Reset
Debug SW
Mode Select
STLINK-V3SET
Pilot Lamp
Bypass Capacitor
MCU
Encoder
DIP SW
STLINK CN

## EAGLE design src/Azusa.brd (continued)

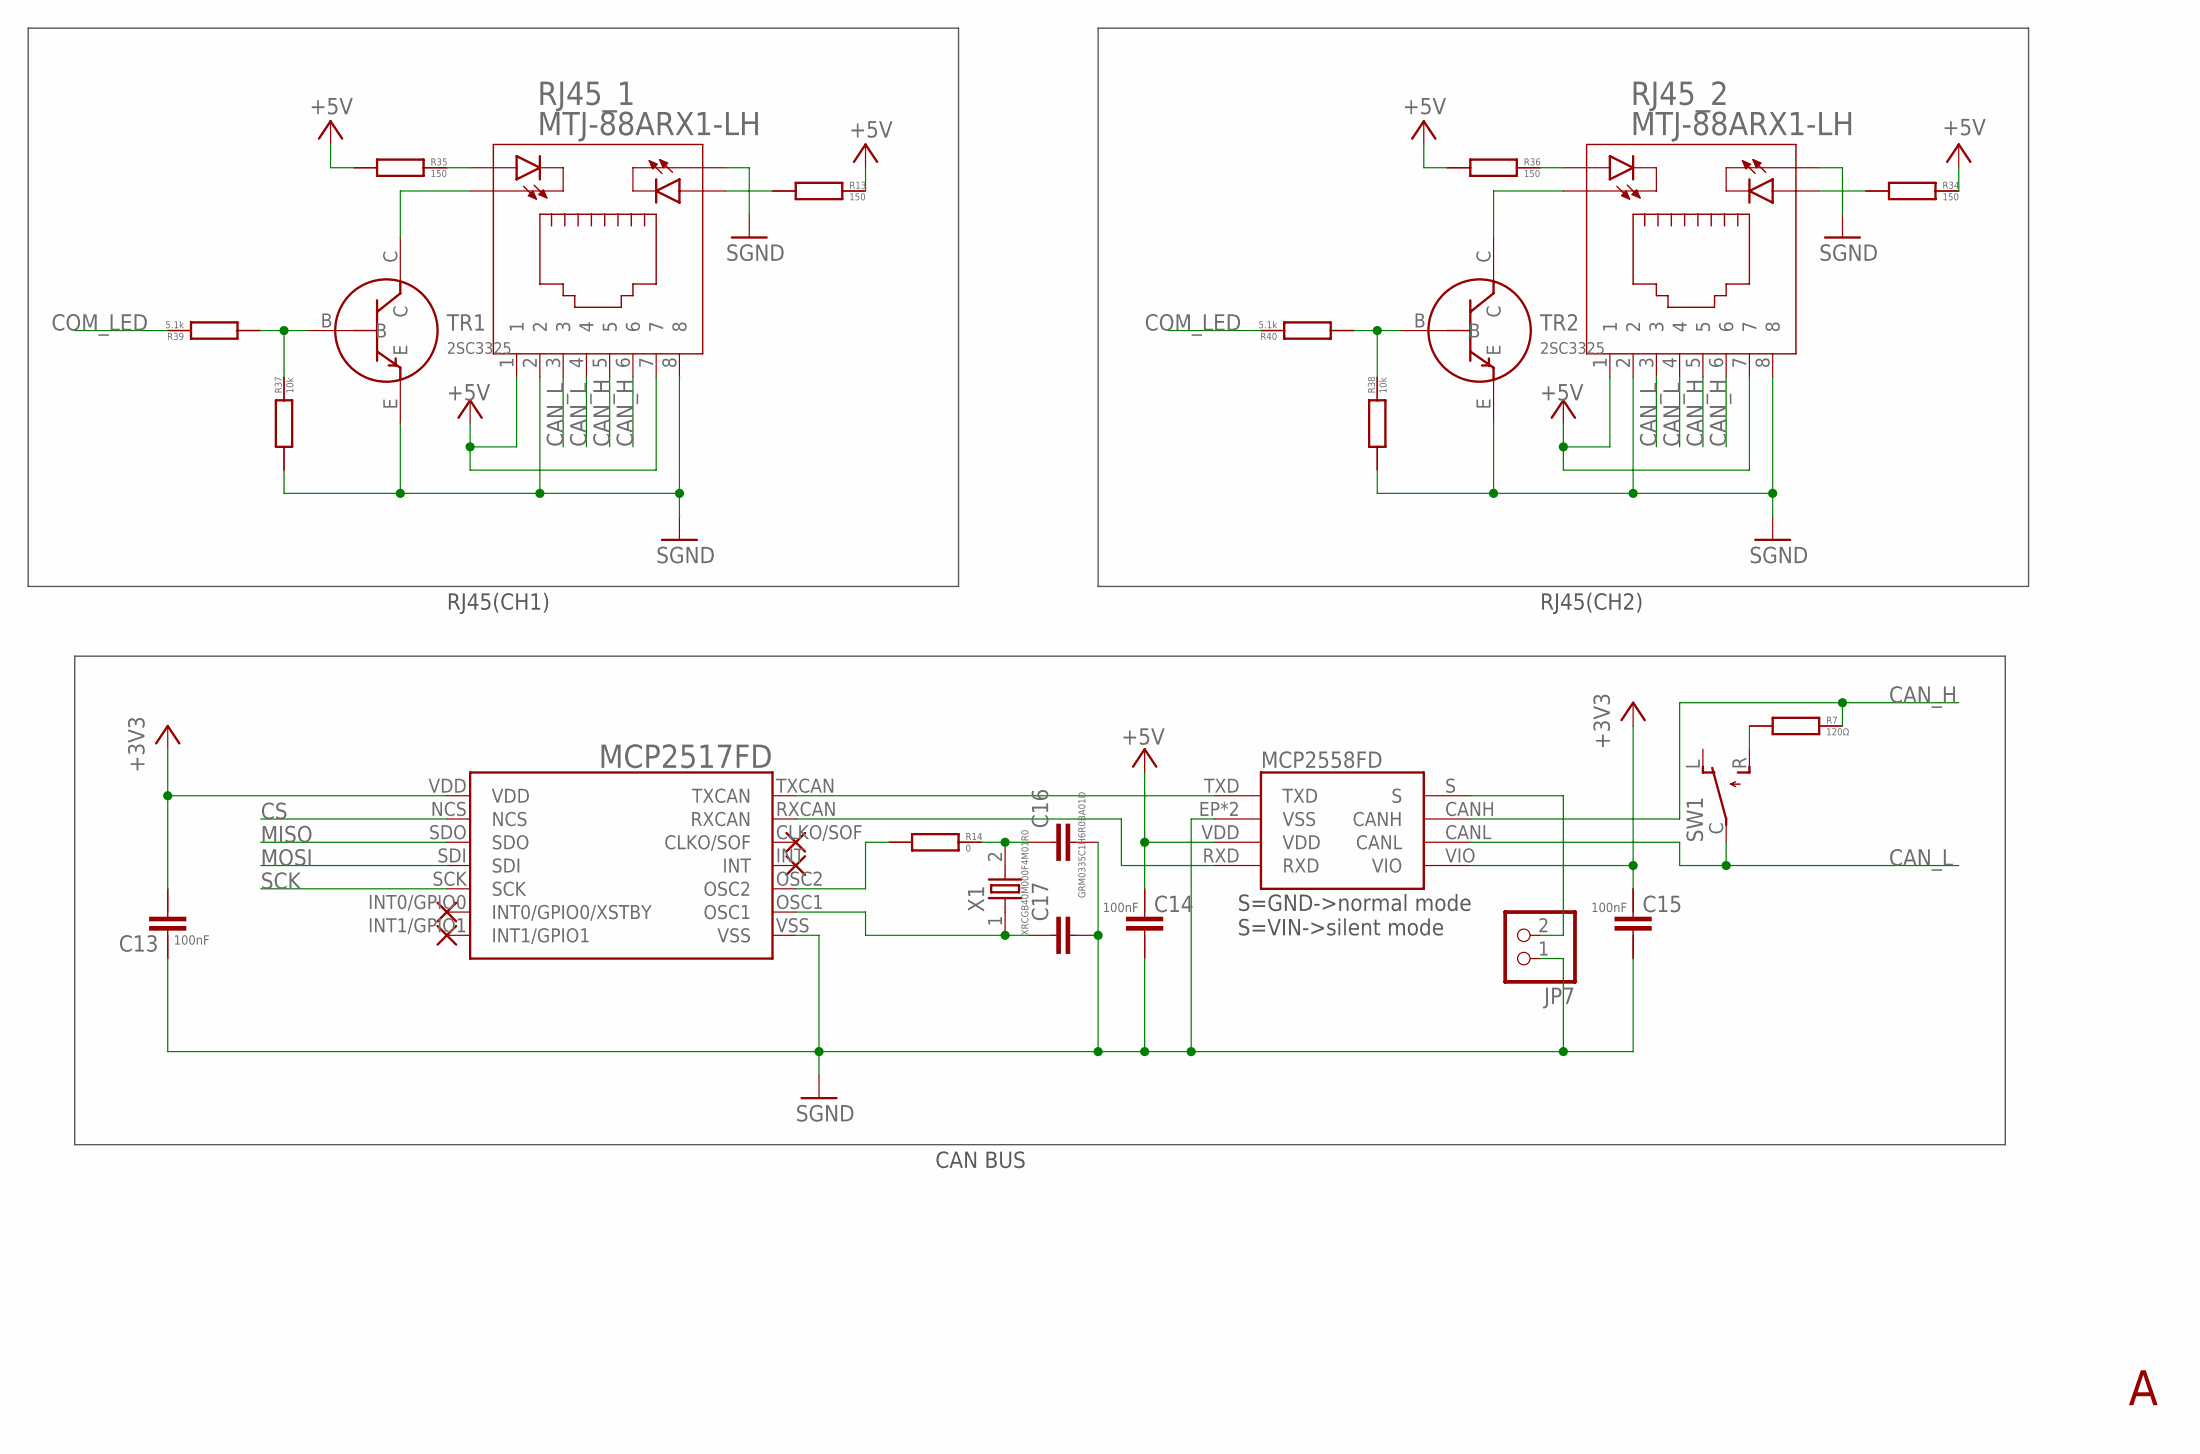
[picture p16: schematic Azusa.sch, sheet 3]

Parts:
C13, C14, C15: GCM188L81H104KA57
C16, C17: GRM0335C1H6R0BA01D; GRM0335C1H120GA01
JP7: PINHD-1X2; 1X02
R7: 120Ω; CR0603
R13, R34, R35, R36: 150; CR0603
R14: 0; CR0603
R37, R38: 10k; CR0603
R39, R40: 5.1k; CR0603
RJ45_1, RJ45_2: MTJ-88ARX1-LH
SW1: SS-12SDP2
TR1, TR2: 2SC3325
U2: MCP2517FD
U$1: MCP2558FD
X1: XRCGB40M000F4M01R0; XRCGB40M000F4M00R0

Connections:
+3V3: C13.P$2, C15.P$1, U2.VDD, U$1.VIO; also elsewhere on the board
+5V: C14.P$1, R13.RIGHT, R34.RIGHT, R35.LEFT, R36.LEFT, RJ45_1.1, RJ45_1.7, RJ45_2.1, RJ45_2.7, U$1.VDD; also elsewhere on the board
CAN_H: R7.RIGHT, RJ45_1.5, RJ45_1.6, RJ45_2.5, RJ45_2.6, U$1.CANH
CAN_L: RJ45_1.3, RJ45_1.4, RJ45_2.3, RJ45_2.4, SW1.C, U$1.CANL
COM_LED: R39.RIGHT, R40.RIGHT; also elsewhere on the board
CS: U2.NCS; also elsewhere on the board
MISO: U2.SDO; also elsewhere on the board
MOSI: U2.SDI; also elsewhere on the board
unnamed: R7.LEFT, SW1.R
unnamed: U2.TXCAN, U$1.TXD
unnamed: U2.RXCAN, U$1.RXD
unnamed: R14.LEFT, U2.OSC2
unnamed: C17.1, U2.OSC1, X1.1
unnamed: C16.1, R14.RIGHT, X1.2
unnamed: R13.LEFT, RJ45_1.LED2_A
unnamed: R34.LEFT, RJ45_2.LED2_A
unnamed: JP7.2, U$1.S
unnamed: R35.RIGHT, RJ45_1.LED1_A
unnamed: R36.RIGHT, RJ45_2.LED1_A
unnamed: RJ45_1.LED1_K, TR1.C
unnamed: RJ45_2.LED1_K, TR2.C
unnamed: R38.RIGHT, R40.LEFT, TR2.B
unnamed: R37.RIGHT, R39.LEFT, TR1.B
SCK: U2.SCK; also elsewhere on the board
SGND: C13.P$1, C14.P$2, C15.P$2, C16.2, C17.2, JP7.1, R37.LEFT, R38.LEFT, RJ45_1.2, RJ45_1.8, RJ45_1.LED2_K, RJ45_2.2, RJ45_2.8, RJ45_2.LED2_K, TR1.E, TR2.E, U2.VSS, U$1.EP (VSS), U$1.VSS; also elsewhere on the board

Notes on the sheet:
S=GND->normal mode S=VIN->silent mode
RJ45(CH1)
RJ45(CH2)
CAN BUS

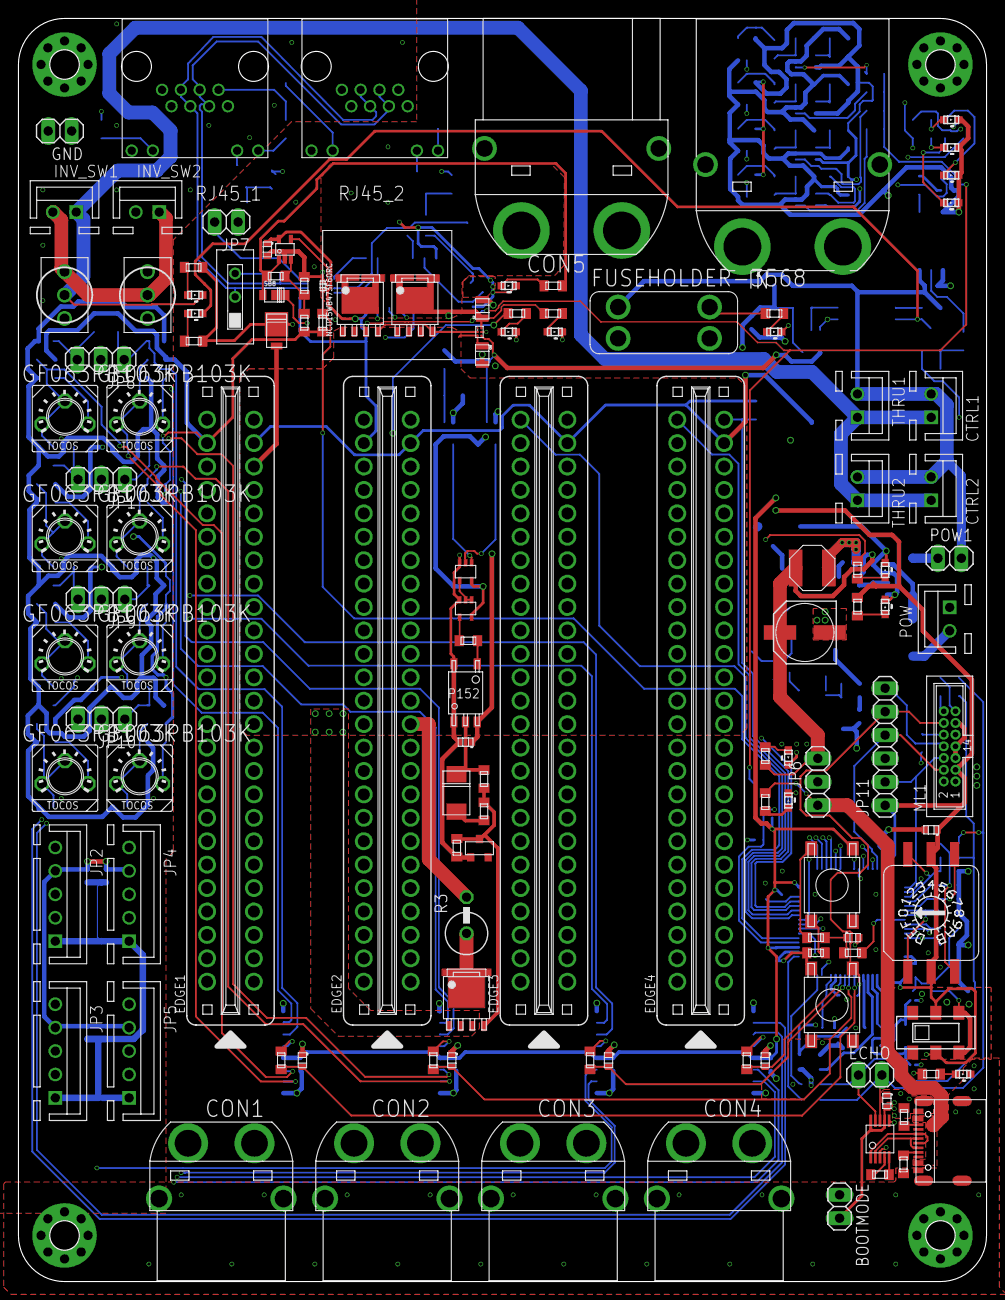
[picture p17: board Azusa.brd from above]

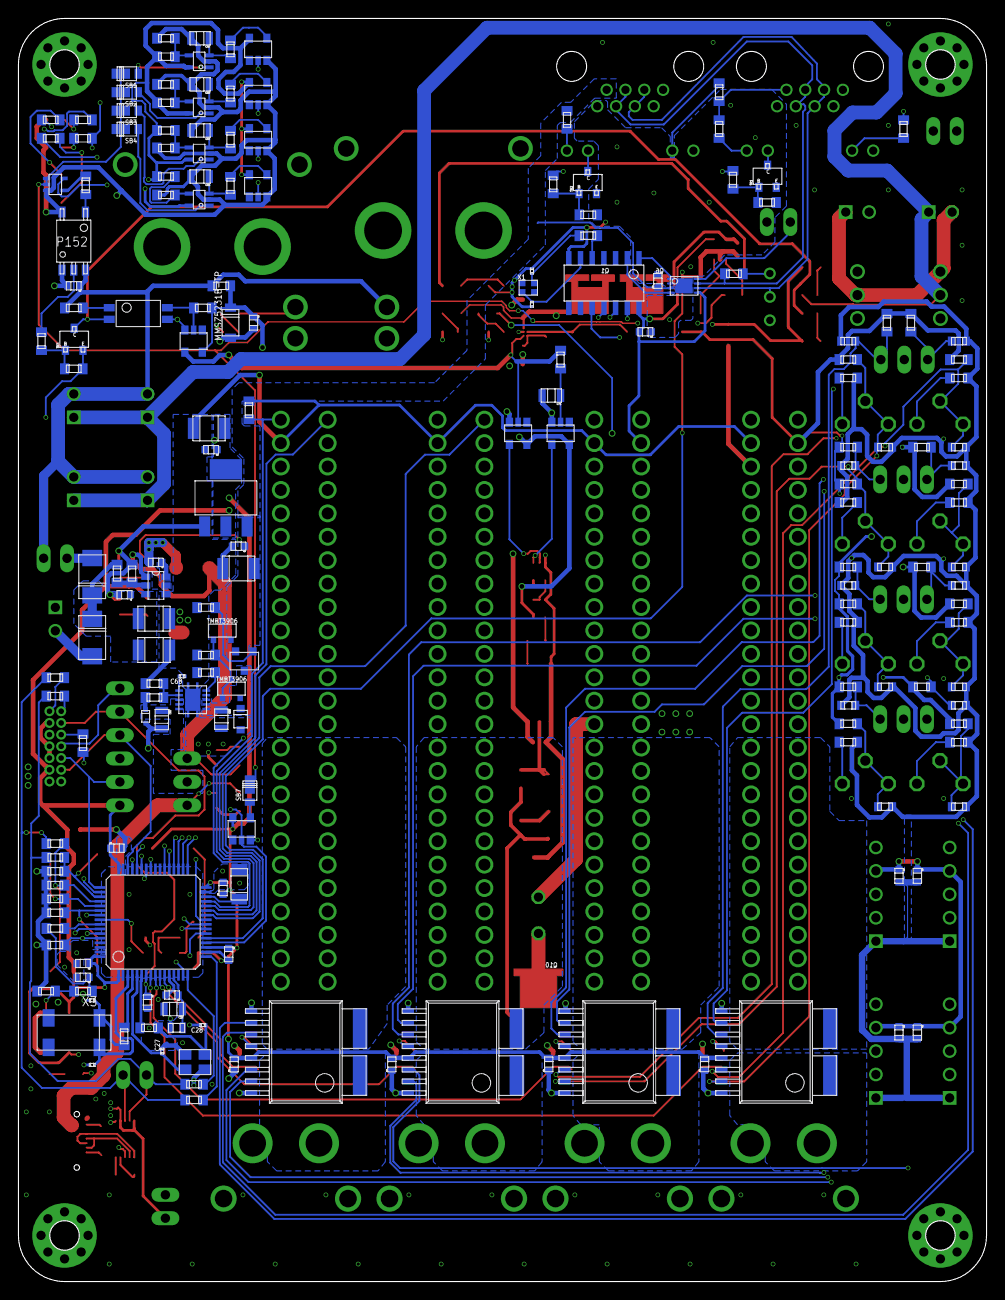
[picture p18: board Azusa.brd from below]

Board: 4 copper layers, 105.0 x 137.0 mm, 315 parts (187 on the bottom side), 207 nets.

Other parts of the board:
HEATSINK1: V2020B

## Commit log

2022-06-18 部品の配置
    [2022年度回路班_新電源基板.brd, 2022年度回路班_新電源基板.sch]
2022-06-18 配線の追加
    [2022年度回路班_新電源基板.brd, 2022年度回路班_新電源基板.sch]
2022-06-19 ベタの追加
    [2022年度回路班_新電源基板.brd]
2022-06-21 DRCエラーの解消
    [2022年度回路班_新電源基板.brd]
2022-06-21 配線完了
    [2022年度回路班_新電源基板.brd]
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2022-06-21 配線完了,KiCadへの移行の前段階
    [2022年度回路班_新電源基板.brd]
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2022-06-21 KiCADへの移行
    [2022年度回路班_新電源基板.brd, 2022年度回路班_新電源基板.kicad_pcb, 2022年度回路班_新電源基板.sch]
2022-06-22 QRコードの拡大
    [2022年度回路班_新電源基板.kicad_pcb]
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2022-06-22 KiCadへの移行前 ネジ穴の追加 conflictの解消
    [2022年度回路班_新電源基板.brd]
2022-06-22 KiCadへの移行 QRコードの追加
    [2022年度回路班_新電源基板.brd, 2022年度回路班_新電源基板.kicad_pcb, 2022年度回路班_新電源基板.sch]
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2022-06-23 エラーの解消
    [2022年度回路班_新電源基板.kicad_pcb]
2022-06-23 基板デザインの完成
    [2022年度回路班_新電源基板.kicad_pcb]
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2022-06-25 名前の変更、ガーバ,ドリルデータの追加
    [2022年度回路班_新電源基板-B_Mask.gbr, 2022年度回路班_新電源基板-B_Paste.gbr, 2022年度回路班_新電源基板-B_SilkS.gbr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]
2022-06-25 gerberの名前の変更
    [PowerUnit-Bseries(ver1.0)-B_SilkS.gbr, PowerUnit-Bseries(ver1.0)-Bottom.gbr, PowerUnit-Bseries(ver1.0)-Edge_Cuts.gbr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]
2022-06-25 再設計 Edgeコネクタを40Pにした
    [2022年度回路班_新電源基板.brd, 2022年度回路班_新電源基板.sch, PowerUnit-Bseries(ver1.0).brd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]
2022-06-25 基盤デザインの完成 gerber出力
    [PowerUnit-Bseries(ver1.0)-B_Mask.gbr, PowerUnit-Bseries(ver1.0)-B_Paste.gbr, PowerUnit-Bseries(ver1.0)-B_SilkS.gbr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]
2022-06-26 基「板」デザインの完成 gerber出力
    [PowerUnit-Bseries(ver1.0).kicad_pcb]
2022-06-26 前バージョンへの移行
    [PowerUnit-Bseries(ver1.0)-B_SilkS.gbr, PowerUnit-Bseries(ver1.0)-Bottom.gbr, PowerUnit-Bseries(ver1.0)-Edge_Cuts.gbr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]
2022-07-06 デザインの修正
    [PowerUnit-Bseries(ver1.0).kicad_pcb]
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2022-09-28 markdownの更新
    [(Eagle)PowerUnit-Bseries(ver1.0).brd, (Eagle)PowerUnit-Bseries(ver1.0).sch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]
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2022-12-21 XT60PWコネクタに変えた
    [(Eagle)PowerUnit-Bseries(ver1.0).brd, (Eagle)PowerUnit-Bseries(ver1.0).sch]
2022-12-22 トランシーバ選定途中、XT60PW
    [(Eagle)PowerUnit-Bseries(ver1.0).brd, (Eagle)PowerUnit-Bseries(ver1.0).sch]
2022-12-23 CANトランシーバの選定(クリスマスイブですよ？（笑）)
    [(Eagle)PowerUnit-Bseries(ver1.0).brd, (Eagle)PowerUnit-Bseries(ver1.0).sch]
2022-12-25 CAN周りの配線など
    [(Eagle)PowerUnit-Bseries(ver1.0).brd, (Eagle)PowerUnit-Bseries(ver1.0).sch]
2022-12-26 レギュレータの追加など
    [(Eagle)PowerUnit-Bseries(ver1.0).brd, (Eagle)PowerUnit-Bseries(ver1.0).sch]
2022-12-27 5Vレギュレータの追加など
    [(Eagle)PowerUnit-Bseries(ver1.0).brd, (Eagle)PowerUnit-Bseries(ver1.0).sch]
2022-12-28 理想ダイオード回路(ディスクリート)の追加
    [(Eagle)PowerUnit-Bseries(ver1.0).brd, (Eagle)PowerUnit-Bseries(ver1.0).sch]
2022-12-29 5VDCDCのMLCC選定、電源回りの整理
    [(Eagle)PowerUnit-Bseries(ver1.0).brd, (Eagle)PowerUnit-Bseries(ver1.0).sch]
2022-12-30 5VDCDCの出力コンをOSコンにした
    [(Eagle)PowerUnit-Bseries(ver1.0).brd, (Eagle)PowerUnit-Bseries(ver1.0).sch]
2022-12-30 +5V周りの冗長性を高める回路を構成(大晦日ですよ？（笑）)
    [(Eagle)PowerUnit-Bseries(ver1.0).brd, (Eagle)PowerUnit-Bseries(ver1.0).sch]
2023-01-05 CANコントローラのXtal選定
    [(Eagle)PowerUnit-Bseries(ver1.0).brd, (Eagle)PowerUnit-Bseries(ver1.0).sch]
2023-01-05 トランシーバ部分の設計終わり(仮)
    [(Eagle)PowerUnit-Bseries(ver1.0).brd, (Eagle)PowerUnit-Bseries(ver1.0).sch]
2023-01-06 STM32の電源回り
    [(Eagle)PowerUnit-Bseries(ver1.0).brd, (Eagle)PowerUnit-Bseries(ver1.0).sch]
2023-01-08 OSC周り
    [(Eagle)PowerUnit-Bseries(ver1.0).brd, (Eagle)PowerUnit-Bseries(ver1.0).sch]
2023-01-09 DIPスイッチ周り
    [(Eagle)PowerUnit-Bseries(ver1.0).brd, (Eagle)PowerUnit-Bseries(ver1.0).sch]
2023-01-14 RJ45の追加
    [(Eagle)PowerUnit-Bseries(ver1.0).brd, (Eagle)PowerUnit-Bseries(ver1.0).sch, (Eagle)PowerUnit-Bseries(ver1.0)_bak.brd]
2023-01-15 電流センサ周りの回路
    [(Eagle)PowerUnit-Bseries(ver1.0).brd, (Eagle)PowerUnit-Bseries(ver1.0).sch]
2023-02-10 電源制御系周り
    [(Eagle)PowerUnit-Bseries(ver1.0).brd, (Eagle)PowerUnit-Bseries(ver1.0).sch]
2023-02-11 ヒューズ選定
    [(Eagle)PowerUnit-Bseries(ver1.0).brd, (Eagle)PowerUnit-Bseries(ver1.0).sch]
2023-02-17 DGND未選別のところまで
    [(Eagle)PowerUnit-Bseries(ver1.0).brd, (Eagle)PowerUnit-Bseries(ver1.0).sch]
2023-03-07 2023/03/07 信号ラインの配線途中
    [(Eagle)PowerUnit-Bseries(ver2.0).brd, (Eagle)PowerUnit-Bseries(ver2.0).sch]
2023-03-08 2023/03/08 sintyoku
    [(Eagle)PowerUnit-Bseries(ver2.0).brd]
2023-03-09 2023/03/09進捗分
    [(Eagle)PowerUnit-Bseries(ver2.0).brd]
2023-03-10 2023/03/10の進捗
    [(Eagle)PowerUnit-Bseries(ver2.0).brd, (Eagle)PowerUnit-Bseries(ver2.0).sch]
2023-03-20 2023/03/20の進捗
    [(Eagle)PowerUnit-Bseries(ver2.0).brd, (Eagle)PowerUnit-Bseries(ver2.0).sch]
2023-03-21 2023/03/21の進捗
    [(Eagle)PowerUnit-Bseries(ver2.0).brd]
2023-03-23 2023/03/23 配線終了
    [(Eagle)PowerUnit-Bseries(ver2.0).brd]
2023-03-23 DRC OK,before I move it KiCad.
    [(Eagle)PowerUnit-Bseries(ver2.0).brd]
2023-03-23 Kicadへの移行後
    [(Eagle)PowerUnit-Bseries(ver2.0).brd, (Eagle)PowerUnit-Bseries(ver2.0).kicad_pcb, (Eagle)PowerUnit-Bseries(ver2.0).kicad_sch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]
2023-03-24 3dmodel top
    [10046971-019LF--3DModel-STEP-533217.step, 2MS1-T1-B4-VS2-Q-E-S.stp, 3568.step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]
2023-03-25 シルク 裏面 2023/03/25進捗分
    [BLM18KG121TN1D.step, CZ-37xx Serie Current Sensor.stp, LQFP64-10x10mm.step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]
2023-03-26 2023/03/26途中(1)
    [1SS404,H3F.step, AP63205WU-7.step, CR_SOD-523_PNJ.step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]
2023-03-26 3Dモデル当て終了
    [XRCGB40M000F1S2KR0_MUR.step]
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2023-03-30 基板微修正、JLCPCBロゴ追加
2023-04-05 微修正失敗(1.524mm)
    [(Eagle)PowerUnit-Bseries(ver2.0)-B_Cu.gbr, (Eagle)PowerUnit-Bseries(ver2.0)-B_Mask.gbr, (Eagle)PowerUnit-Bseries(ver2.0)-B_Paste.gbr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]
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

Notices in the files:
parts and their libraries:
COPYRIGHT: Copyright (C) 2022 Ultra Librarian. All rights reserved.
